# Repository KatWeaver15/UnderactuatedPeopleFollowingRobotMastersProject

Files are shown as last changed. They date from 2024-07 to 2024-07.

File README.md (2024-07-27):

# UnderactuatedPeopleFollowingRobotMastersProject
This repository contains documentation of an underactuated person following robot that utilizes UWB for a masters capstone project.

The software for project is still an ongoing endeavour, the source code is not included in this github repository at this time.

This robot was designed between 2022 and 2023 under both Dr. Liwen Shih (Capstone Advisor) and Dr. Harman (Mobile Robots Course CENG 5437) at UHCL. 

## Motivations

The motivation of this project is to develop an autonomous, person following robot that can carry objects while someone is performing activities in both an outdoor or indoor setting and on smooth or rough terrain.  The robot that was developed by the end of this project is only a prototype and isn't designed for manufacturing.  It's more of a robust frame that can hold enough sensors, and other internal modules to testbed different software solutions.  

## Design Overview
The robot was designed to be able to follow a person off-roads and in crowded environments.  To achieve this, a two-wheeled underactuated design was chosen to ambulate the vehicle and Ultra-Wideband (UWB) trackers (four DWM3001CDK modules) were used to locate a person to follow using 3D trilateration.  The robot is currently utilizing a raspberry pi with ARM powered peripherals and uses a mixture of UART and USB for intra-robot communication and WiFi, Bluetooth, and UWB for communication with computers and peripherals outside the robot.  PID and linearized state equation solutions (LQR) were investigated for controlling robot movement.  Sensor fusion solutions utilizing complementary and kallman filters were investigated to provide data to control solutions.  A PID solution was used to control two BLDC motors to power the wheels and used feedback from rotary encoders.  ROS was used to organize the code for the robot and for simulation.  FEA in Autodesk Inventor was used to iteratively test small changes in chassis frame parts to test for deformation under load.  OpenSCAD was used to programmatically generate pulley designs for use in the robots pulley system.  White PLA was used for the chassis and black flexible TPU was used for the wheels.  An OAK-D Series 2 camera system was used to implement SLAM for navigation and obstacle avoidance using stereo depth perception.  Both Python, C++, and C were used to program the robot and its peripherals.  Docker was used to containerize and test ROS modules in a desktop environment and allowed for the easy transfer of modules from desktop to robot environments.  The total cost of the robot was about 2100$.

Several renders are shown below.
Internal Cutaway | External Cutaway
--- | ---
Internal Cutaway | External Cutaway

Several design issues that would need to be changed in a re-design of this robot would include, but not be limited to the following:
  1. The use of a Phase-Difference of Arrival (PDOA) UWB tracking system.  This type of UWB tracking scheme is much more compact than Time-of-Flight (TOF) UWB tracking.  Unfortunately, commercial modules for PDOA tracking are an order of magnitude more expensive than TOF UWB tracking modules.
  2. The use of other manufacturing materials and methods besides FDM 3D printing.  The sole use of FDM printing (due to a lack of alternatives, such as subtractive techniques) drove up the final materials cost significantly.
  3. The inclusion of an adjustable and/or smaller volume gearing/belt system.  The belt system included in this robot was designed to conform to the load and speed requirements during the conception of this project, but in retrospect the produced design is bulky and cannot be changed if a different motor choice is desired.
  4. While robust, the wheels on this robot are very heavy (50% infill).  This necessitates slow acceleration of the robot.  Additionally, too fast of an acceleration will cause the chassis to spin instead of the wheels when the robot begins to move from rest.  The solution to this problem is to reduce the mass of the wheels.  The reason this issue was not caught during the initial design of the chassis was that the free body diagrams used to model the robot considered the chassis to be a non-moving entity.  The design issue was caught in simulation, but by then the wheels were already printed.
  5. A more powerful internal processor should be considered.  The raspberry pi was not adequate for performing SLAM using ROS as well as other control tasks using the current software.
  6. The O-Drive used to power the BLDC motors is bulky and takes up lots of space.  Additionally, the hardware interface uses GPIO pins that can shake loose during robot operation.  A custom solution would be more adequate for a finalized design of this robot.
  7. Flexible, 3D printable TPU was used to line the wheels, but due to low friction led to slippage and errors in odometry measurements.  A cast solution using 3D printed moulds and a small vacuum  chamber would be a better choice of material for wheel linings.
  8. The OAK-D series 2 stereo cameras have a low resolution (1MP, 1280x800, global shutter) and while the framerate is adequate (120 FPS for stereo cameras) it is not very good at detecting fast moving obstacles far away from the robot (people running at the robot, cars, etc.).  While the OAK-D series 2 module is an economical solution, the cost is prohibitive to place modules on each side (4 sides) of the robot (200$ per module).  Examples of a higher-performing and economical solution would be to use new distance measurement methods using high resolution, low cost, rolling shutter camera modules as well as low-cost LIDAR modules (that are not available for individual commercial use). 
  
## Part/Design Selection
A trade off analysis was performed when choosing the motors, drive scheme, tracking methods, distance measurement sensors, cameras for visual SLAM, encoders, small computers, and encoders in to assist in the implement of this design.

### Motor Selection
After considering different motor types, a BDLC motor was chosen to power the robot due to its efficiency, weight, and noise.  Due to low torque from a BLDC, a gearing or belt system would need to be designed.  Closed loop feedback can easily be performed using an encoder attached to the output shaft.  If backlash is big enough problem, a dual feedback scheme can be used where a high speed magnetic encoder, or similar high-speed encoder, can be attached to the BLDC motor (input shaft) in addition to the encoder attached to the output shaft.  
The finished design did have significant backlash from loose connections between the wheel and wheel attachment point.  This was fixed by printing a tighter fitting connector.
A custom-made axial flux motor solution would be an ideal choice for this robot (higher power density, lower volume), but would greatly increase development time.

### Drive Scheme Selection
Different steering mechanisms were considered, but a differential, two-wheel self-balancing robot with a low center of gravity was chosen because of its simple odometry (differential drive), interesting design, and good turning characteristics.  In addition to this, there has been, historically, a large number of people who have also constructed this kind of robot (an inverted pendulum model) for people follower robots, enabling this robot to potentially draw from a large number of readily available technical resources.  This design is also well suited for outdoor environments due to its high ground clearance and large wheels.

### Tracking Methods
Several UWB sensors were chosen to be used to track a user due to their simplicity and readily availability at a low price.  Other close contenders were Bluetooth and WLAN methods, but each of these methods were not purpose built specifically for tracking and would be harder to implement effectively.  Other methods investigated were divided into camera and non-camera based methods.  Camera methods, like those used in the Gita series of people following robots, include Feature Based Tracking, Feature Based learning, and Deep Learning.  Non-camera based methods investigated included IMU based tracking, GPS, RFID, WiFi, Bluetooth, and UWB.

### Distance Measurement Sensors
A stereo/monocular based solution with paired IMU was chosen due to its ready availability (compared to 3D LIDAR sensors), low comparative cost to methods of comparable effectiveness (LIDAR/RADAR), longer detection range compared to SONAR, and greater effectiveness in sunlight compared to IR sensors.

### Camera Selection
After much consideration, the Oak-d s2 was chosen due to its higher resolution stereo cameras (1280x800 px) at a high framerate (120 fps) at a reasonable price (200$), which was cheaper than purchasing two better individual camera modules that had both global shutters and sync pins.  It’s also noted that there are several cheaper options for comparable stereo camera modules, but there were less examples on how to use these cameras (less documentation), so the camera module with a higher amount of support was chosen.

### Encoder Selection
The CUI AMT10E, an incremental 5120 pulse per revolution encoder, was chosen since it was relatively cheap (~25$ each) compared to similarly performing encoders and was easy to implement, unlike a magnetic encoder which would need it’s own custom PCB to implement.  Other designs, such as an optical encoder or low pulse-per-revolution quadrature encoder, were not considered due to being more complex and expensive for the former, and too inaccurate for the later.  Additionally, the CUI encoder could also operate at the maximum output shaft output RPM.

### IMU Selection
Inertial Measurement Units (IMUs) were chosen by calculating the effective number of bits (ENOB) of their accelerometer and gyroscope outputs as well as their Zero-G output, and noise.  A low Zero-G output is needed since it defines the smallest accelerometer and gyroscopic values the IMU can measure.  A low noise value determines how much filtering is needed for the output values.  Lower noise values also mean that smaller samples can be taken from the sensor output.  The ENOB can be estimated using the sensors THD and SNR values.  A higher ENOB value is useful for distinguishing the sensors signal value from noise during filtering.  A BMI 270 module was chosen due to its low cost, decent ENOB, low Zero-G output, and low noise.

## Hardware Design

The robot was designed as a knee-height differential drive robot with a 40cm wheel radius and able to follow a person jogging up to about 8 mph.  The chassis and wheels are to be printed by a 3D-printer in PLA, while the wheels were designed to be printed in TPU, a flexible 3D-printable filament.  A simplified diagram of the robot is shown below.  Another DWM3001 module was used to trilaterate user positions relative to the robot.



### Motor Selection
Motor selection was performed by first calculating the torque requirements to move the robot from rest since the coefficient of static friction is greater than the coefficient of sliding friction and it takes more energy to get a robot moving than to keep it moving.  In order to find the torque needed to overcome the force exerted by static friction, we had to find the static friction acting against the motor torque by the wheel material at rest. It should be noted that deformation of the TPU material was not considered in this analysis and a 2D free body diagram of the wheel was used in the design.  A more accurate estimation would use a 3D free body diagram that takes the mass of the individual parts of the robot into account instead of the singular total mass of the robot.  

 A paper on the friction properties of TPU was consulted to find friction coefficients of TPU [1].  The characteristic hump that indicates the coefficient of static friction of the TPU material was not found, since TPU is a rubber-like material and the coefficient of rubber-like materials is greatly dependent on the load, temperature, loading conditions and lubrication of said material [2].  Thus, the maximum value of sliding friction found for TPU in [1], 1.5, was doubled to 3 to estimate the force required to move the robot with a wheel radius of 0.2m from rest.  The plotted function is Torque = 0.2m(u*n)/2 where u is the coefficient of friction and n is the normal force.

 An estimation of torque needed to move the robot was plotted on a 3D graph with mass and static friction used as independent variables.
 Torque as a function of mass and the coefficient of static friction | Torque as a function of mass
--- | ---
  | 

After consulting the above plots, a maximum load of 20kg was chosen, which corresponds to a torque of 58.86N at a coefficient of static friction of u = 3.  Now that the torque that we need for the output is known, we can then select a motor and gear system to deliver this power to the output.  An informal study was found on the torque of BDLC motors at [3].  Using the formula found on [3], another torque curve was calculated using BLDC kV and current through the motor (it’s important to note that motor kV is not “kilovolts”, but the rpm per volt applied to the motor (rpm/volt)).  The equation for  Torque is about (8.3 * Current) / motor Kv.  The torque curve is shown below.
 Torque as a function of motor kV and current | Side profile view 
--- | ---
 | 

A 190kV motor that advertises that it can output 7.5Nm of torque at 75A was chosen (flipsky hardened 6368 190kv 2700w BLDC electric skateboard motors).

Assuming that 7.5Nm of torque at 75A is accurate and also assuming that the relationship between torque and current is linear, we can assume that at 50A, 5Nm of torque can be delivered by the motor.  At a 12:1 gear ratio the motor can deliver 60N of torque (enough to push a 20kg load from rest) and can move at 190 (rpm/volt)*50V = 9500 rpm.  Then with a 12:1 gear ratio the output speed will have an RPM of 9500/12 = 791.667 RPM, which is greater than the speed we need to drive our robot at 8 mph. 

[1]: B. Pinedo, et. al. “Thermal Analysis and Tribological Investigation on TPU and NBR Elastomers Applied to Sealing Applications”. Tribology International, 17 May 2018.
-A paper describing the properties of TPU and NBR, used to find the static and sliding friction of TPU.

[2]: A. Tuononen. “Onset of frictional sliding of rubber–glass contact under dry and lubricated conditions”, 13 June, 2016. Nature: Scientific Reports.  6, Article number: 27951

[3]: Richard Parsons, December 25, 2018, https://things-in-motion.blogspot.com/2018/12/how-to-estimate-torque-of-bldc-pmsm.html 

### Belt Selection

Pulleys and belts were chosen to use to create the proper gear ratios for this robot due to how quiet they were and low backlash.  A rounded tooth profile was chosen to also reduce noise.  Pulleys sets with 15 tooth to 60 tooth and with 15 tooth to 45 tooth would together give the 12:1 gear reduction ratio to move with our maximum weight.  A 5mm tooth profile was chosen to satisfy our maximum torque requirement to pull 20kg.  The length of each pully was chosen by first calculating the equation for the belt of an arbitrary pulley set and then graphing this equation in python to find a suitable belt length graphically.  The outputs of this are shown below in Figures 1 and 1.  Figure 1 was used to find the timing belt length for a 15 tooth and 60 tooth 5mm pulley and found that a 350cm timing belt would be an appropriate fit for this pully pair with a center distance of about 7.2cm.  Figure 2 performs a similar task with a 15 tooth and 45 tooth pulley pair and finds that the center distance for the chosen pulley belt and pully pair would be about 9.7 cm.  Belts were selected from McMasterCarr.  

Figure 1 | Figure 2
--- | ---
 | 

### Pully Generation

In order to reduce costs, pulleys for this robot were generated in OpenSCAD and the 2D gear profiles were exported to be used in Autodesk Inventor.  From there, the pulleys were designed and printed on an Ender 5 3D printer with PLA filament with a 1mm nozzle.  



### Robot Structure
The physical structure of the robot was designed in Autodesk Inventor and printed on an Ender 5 3D printer using a 1mm nozzle with PLA.
Figure 1 | Figure 2
--- | ---
 | 

### UWB Hardware Implementation

Four DWM1004 UWB modules with integrated STM32L M0+ microcontrollers were initially purchased to find the position of a person relative to the robot.  DWM3001CDK modules were used instead in the final design.
In order to attempt to use the DWM1004 trackers, PCBs were designed in KiCAD and ordered from JLCPCB to use the sensors on a breadboard.  The board is a 4-layer design and ordered with an ENIG finish.  Figure 1 shows the schematic of the PCB, Figure 2 shows the layout of the PCB, Figure 3 shows a rendering of the PCB performed before purchase, and Figure 4 shows the ordered PCB with the sensor soldered to it.  
Figure 1 | Figure 2
--- | ---
 | 

Figure 3 | Figure 4
--- | ---
 | 

### Robot Power System Design

After much consideration, a power system was designed to both protect the user of the robot and the robot itself.  Separate isolated power supplies are used to power both the robot motors and the raspberry pi and associated sensors.  An E-stop system to the power supply for the motors and the BLDC controller are present.  Notice how the red E-stop button uses two relays to control power to the BLDC power supply.  This is to prevent E-stop button failure in case one or more of the wires to the E-stop button are severed.  The E-stop buttons do not stop power to the control circuit so that the control circuit can be shut-off separately and investigated after a motor related failure.  If this was not done then the same motor failure could start once again upon system startup.  The figure below shows a diagram of this setup



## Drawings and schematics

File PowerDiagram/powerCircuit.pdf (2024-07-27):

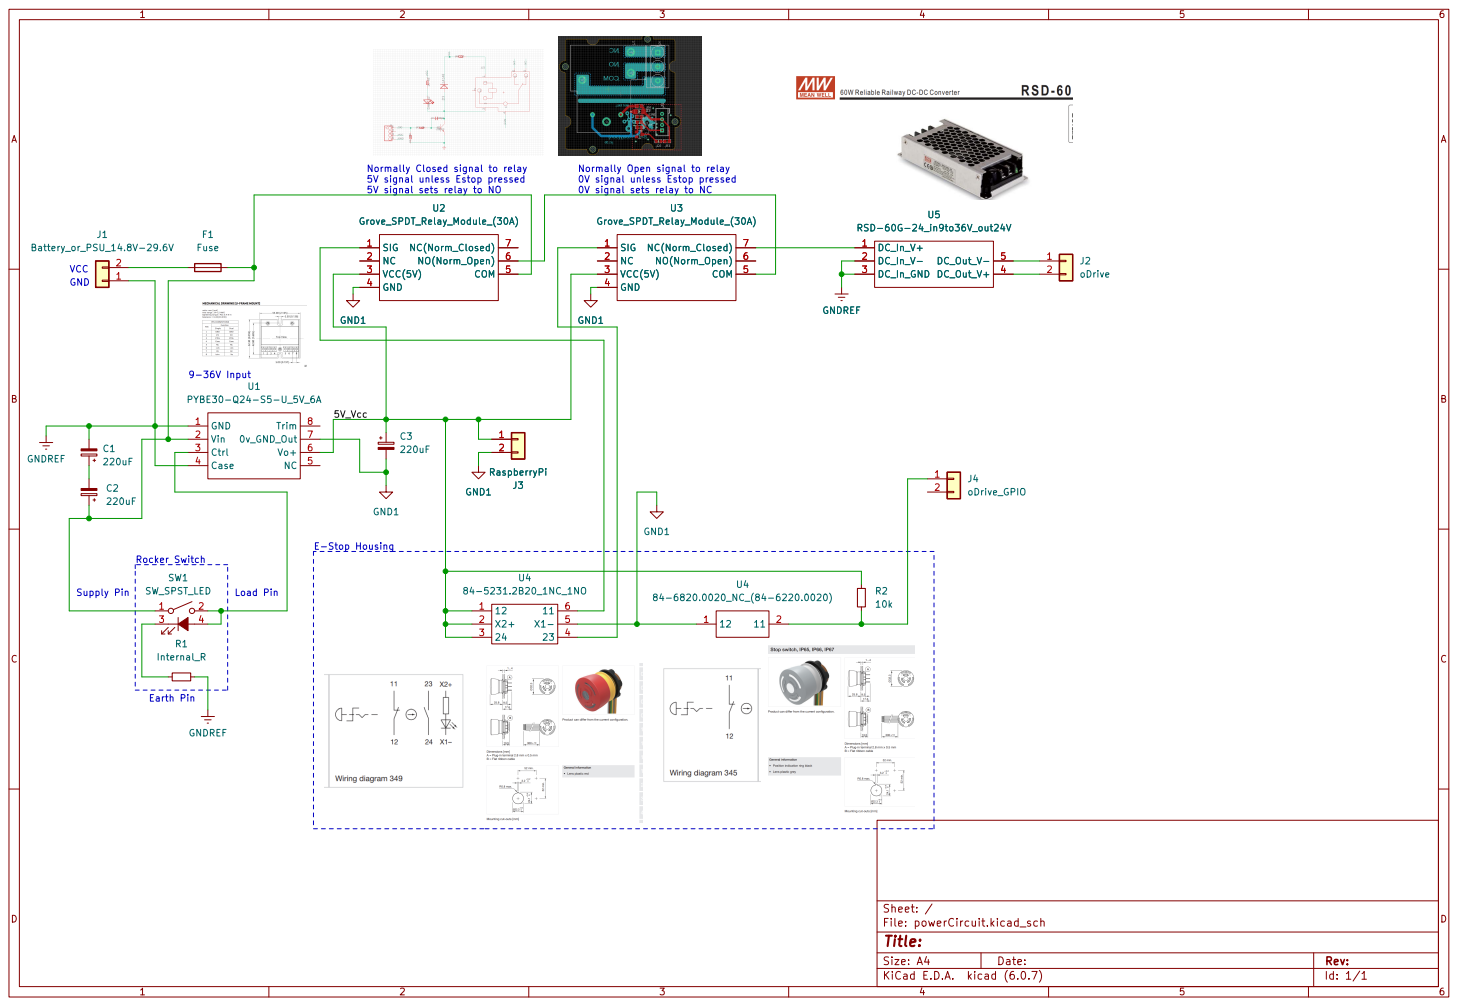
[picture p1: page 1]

5V_VccNormally Closed signal to relay

5V signal unless Estop pressed
5V signal sets relay to NO

0V signal unless Estop pressed
0V signal sets relay to NC
